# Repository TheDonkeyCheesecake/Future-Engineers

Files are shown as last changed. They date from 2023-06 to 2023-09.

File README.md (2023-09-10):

# Engineers Documentation

Repository containing the engineering elements and details of Team Asparagus from Canada, participating in the 2023 WRO Future Engineers competition.
***
## Repository Content

- `models` - 3D printable files designed by us
- `others` - other essential files
- `schemes` - schematics of our robot's electrical systems
- `src` - main and other programs to run/control software
- `t-photos` - one serious and one funny photo
- `v-photos` - photos of our robot from each angle
- `video` - YouTube link of our robot running each program on the game field
***
## Team Members

- Weston Law, 15, [westonlaw@hotmail.com](mailto:westonlaw@hotmail.com)
- Brian Yin, 15, [brianyin256@gmail.com](mailto:brianyin256@gmail.com)
- Eric Rao, 15, [ericrao08@gmail.com](mailto:ericrao08@gmail.com)

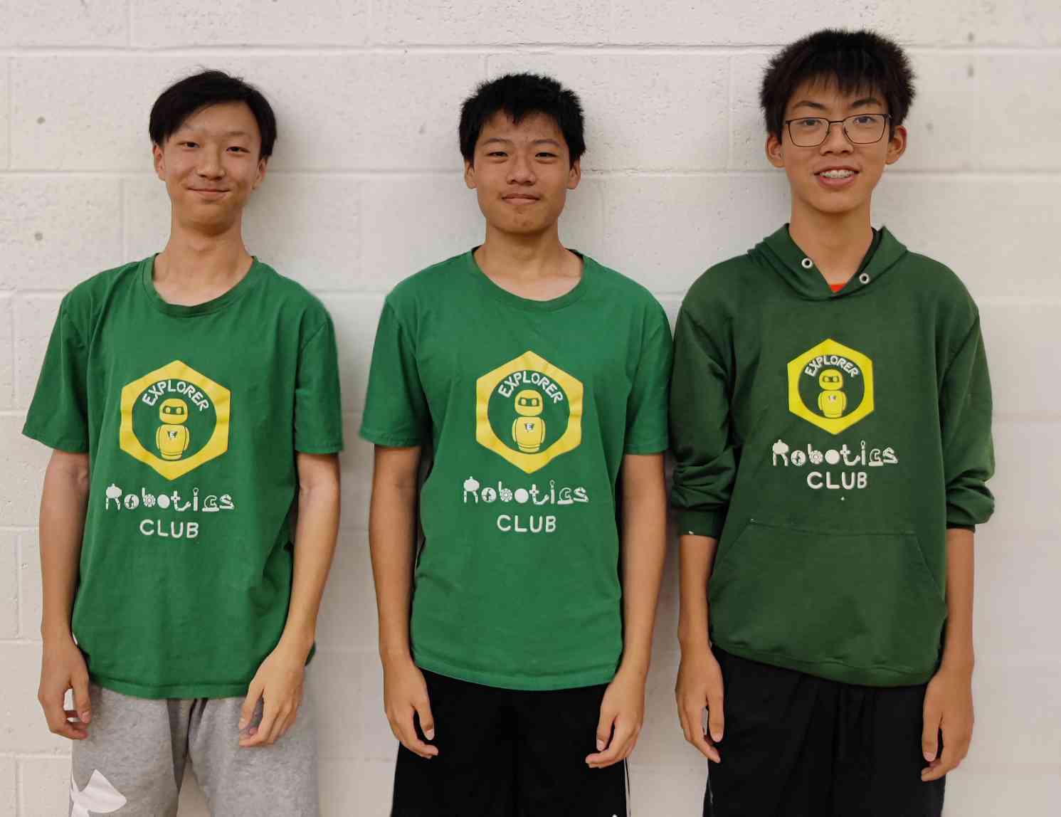
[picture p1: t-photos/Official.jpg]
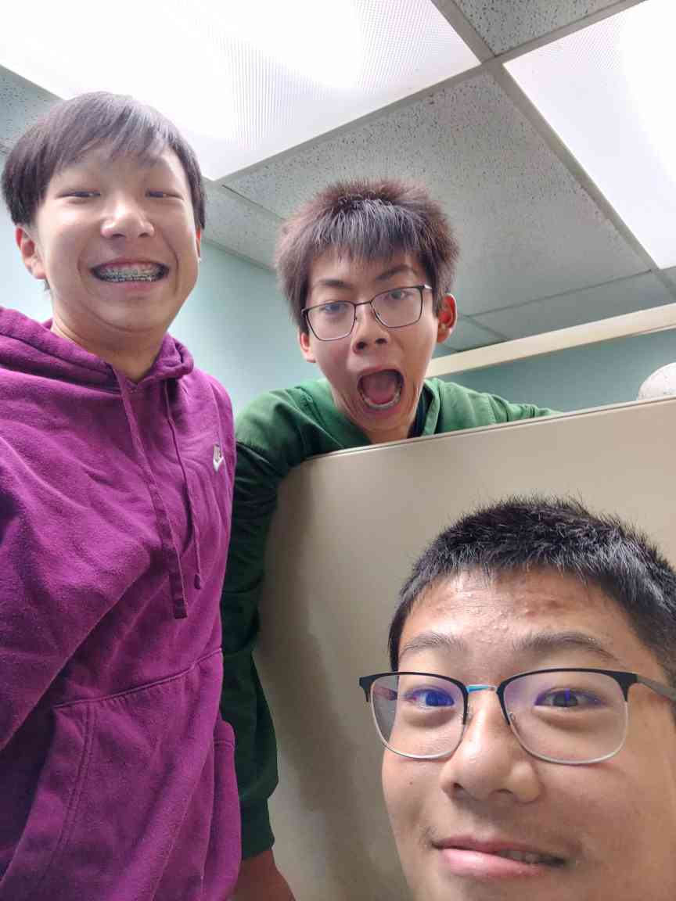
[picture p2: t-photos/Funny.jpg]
 

***Weston (left), Brian (middle), Eric (right)***

***
## Hardware List and Assembly

### Parts List

- [LaTrax Rally RC Car Chassis](https://latrax.com/products/rally)
- [Arduino UNO R3 Controller Board + wires/cables](https://www.amazon.ca/gp/product/B01D8KOZF4/ref=ppx_yo_dt_b_search_asin_image?ie=UTF8&psc=1)
- [Vemico Raspberry Pi 4 Board + Fan](https://www.amazon.ca/gp/product/B09WXRCYL4/ref=ppx_yo_dt_b_search_asin_title?ie=UTF8&psc=1)
- [SanDisk 64GB Ultra microSD Card](https://www.amazon.ca/gp/product/B073JYVKNX/ref=ppx_yo_dt_b_search_asin_title?ie=UTF8&th=1)
- [PiSugar S Pro 5000 mAh Lithium Battery + PiSugar Module Platform Attachment](https://www.amazon.ca/Portable-Platform-Raspberry-Accessories-handhold/dp/B097RCFHD2)
- [HobbyWing Quicrun 2435 4500Kv Brushless Motor](https://www.xtremerc.ca/products/quicrun-wp-10bl60-waterproof-esc-1-10-car-sensorless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)
- [Hobbywing Quicrun WP-16BL30 ESC](https://www.xtremerc.ca/products/hobbywing-quicrun-wp-16bl30-waterproof-1-18th-scale-brushless-esc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)
- [Hosim 7.4V 1600mAh 25C Li-Po Rechargeable Battery](https://www.amazon.ca/Hosim-2pcs-1600mAh-Connector-Li-Polymer/dp/B098QSLJKV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)
- [LoveRPi Wide Angle Camera + CSI Cable](https://www.amazon.ca/gp/product/B07KF6QVPY/ref=ppx_yo_dt_b_search_asin_title?ie=UTF8&psc=1)
- [DKARDU DPST Switch](https://www.amazon.ca/gp/product/B09TKMR8J4/ref=ppx_yo_dt_b_search_asin_title?ie=UTF8&psc=1)

Our 3D-printed parts weigh roughly 75 grams, which is around $2.50 worth of filament. They consist of a platform and pieces to create a camera mount, printed by a Bambu Lab P1P 3D printer.

Total Cost: `$182.84` + `$57.99` + `$229.99` + `$13.36` + `$39.99` + `$49.99` + `$44.99` + `$39.99` + `$13.40` + `$14.49` + `$2.50` respectively = `$689.04` and `$778.61` with tax. (prices in CAD)
***
### Assembly

#### Mobility

We used a prebuilt RC car chassis and made modifications to integrate the rest of our components onto the body of the car, including a new DC motor, a 3D printed platform, and circuit boards (all parts can be found in the Parts List above). In addition, the receiver that allows the car to be controlled remotely was removed, as it was unnecessary and took up space.

The robot moves through two different motors; a `HobbyWing Quicrun 2435 4500Kv Brushless Motor` for driving and a servo motor for steering. The servo motor we use came attached to the prebuilt base, but we changed out the DC motor. The new DC motor is attached similarly to the original, under the 3D printed platform, and takes up roughly the same amount of space. It is held tightly with a metal bracket and screw to prevent it from moving.

We chose this motor as it was one of the highest quality DC motors we could find locally that was of the right size to fit our RC car. This motor provides superior torque to other motors we have tried, an aspect crucial to the function of our car as it helps the car run smoother and avoid cogging at lower speeds. This motor is also brushless meaning higher efficiency and better performance as it doesn't contain the "brushes" that would normally cause friction and reduce the motor's efficiency. 

Unfortunately, even with the higher quality motor, our car still suffers from cogging occasionally when running at low speeds due to the inevitable weight added to the chassis due to our electromagnetic components, which restricts the motor's movement. 

The other component under the platform is the ESC `(electronic speed controller)`, which is wired to and controls the speed of the newly added DC motor. It is also connected to the `Hosim 1600mAh Li-Polymer Battery`, placed right next to it, supplying a sufficient 7.4V.

The motors are controlled by the `Arduino UNO R3 board`, placed on top of the platform using standoffs.

To connect the Arduino, ESC, DC motor, and servo motor, we use a custom-designed perfboard which all the wires plug into to form a circuit. The Arduino uses two PWM `(pulse width modulation)` ports to control the signals sent to both of the motors and an additional port to ground the circuit. The motors use 3 ports/wires each for power, signal, and ground. 

The DC motor is wired to and receives power directly from the ESC (which is connected to the battery), but the servo motor receives it from a BEC `(battery eliminator circuit)` inside the ESC, which is designed to provide a regulated and constant voltage supply to power low-power electronics, such as the servo motor.
***
#### Power and Sensing

Beside the Arduino Board is the `Vemico Raspberry Pi 4 Board`, along with a fan for cooling and a `SanDisk 64GB Ultra microSD Card` to hold our programs. Wired and mounted on top of it is the `PiSugar Module Platform Attachment`, which also is fed power from the `PiSugar S Pro 5000 mAh Lithium Battery`. The battery provides 3.7V, which is then converted to 5V using a voltage regulator to meet the operating voltage requirement of the Raspberry Pi.

We use two separate batteries for the ESC and Raspberry Pi to manage their battery lives independently, as they have different power/voltage requirements. It avoids the problem of having one circuit taking too much power from the battery and leaving an inadequate amount for the other.

The last component is the `LoveRPi Wide Angle Camera`, which is mounted with the help of a custom 3D-printed stand and is wired to the Raspberry Pi through a CSI cable. Although it is more complicated to use, we decided it would be more power-efficient than multiple ultrasonic/colour sensors.

The Raspberry Pi is placed on top of a black box frame specifically made for it, holding it squarely in place, while also housing the fan inside to prevent the Raspberry Pi from overheating.

A `DPST switch` connects to the circuits of both the Raspberry Pi and the ESC, making it possible to turn on both the Raspberry Pi and ESC with one switch. This was done to satisfy the condition of having one power switch to turn on all the components of the car.

#### Photos
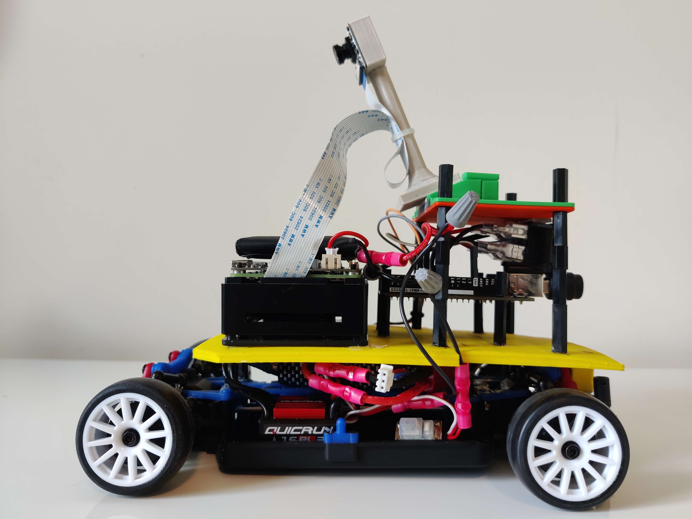
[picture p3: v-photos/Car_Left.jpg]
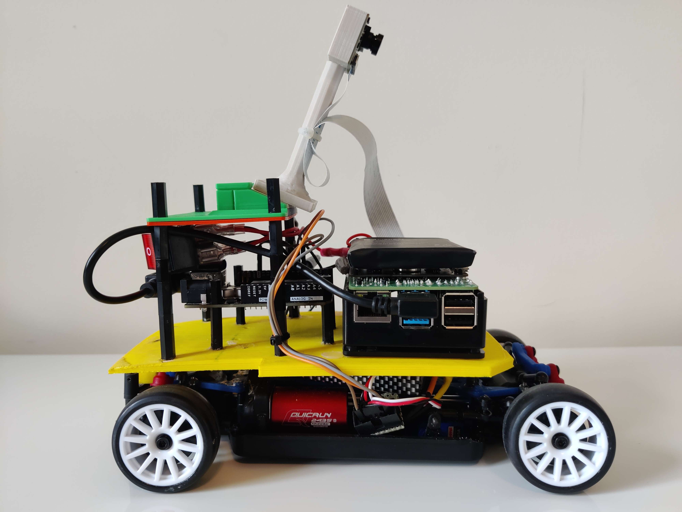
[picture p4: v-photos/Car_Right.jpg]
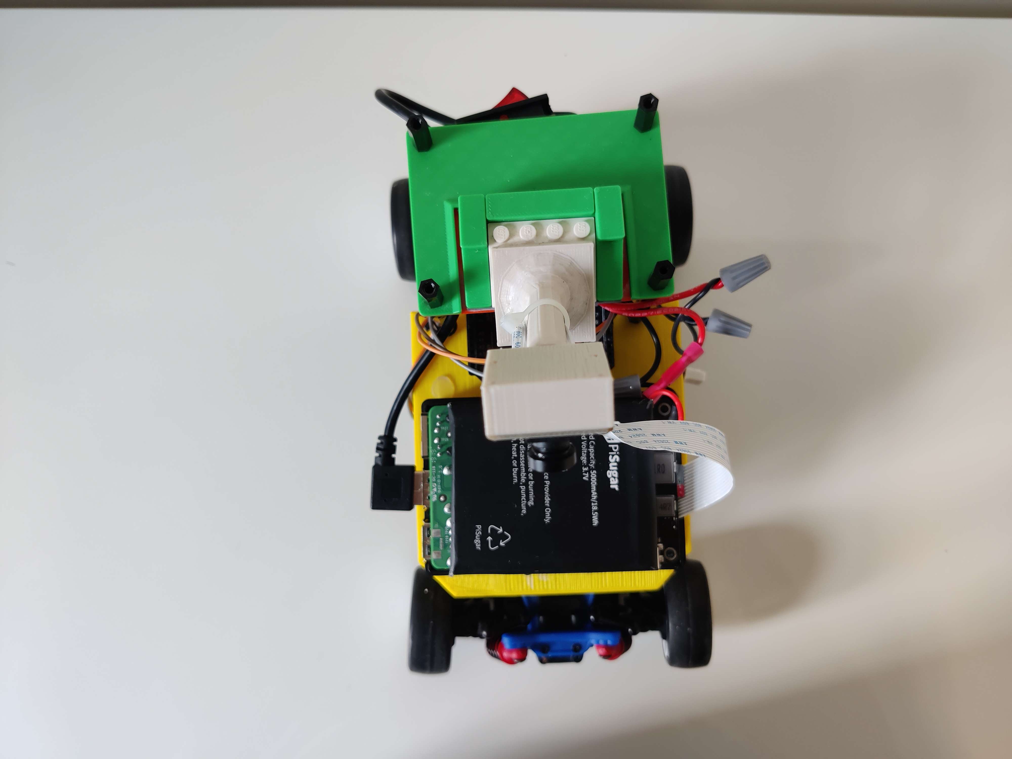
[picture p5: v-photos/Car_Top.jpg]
  

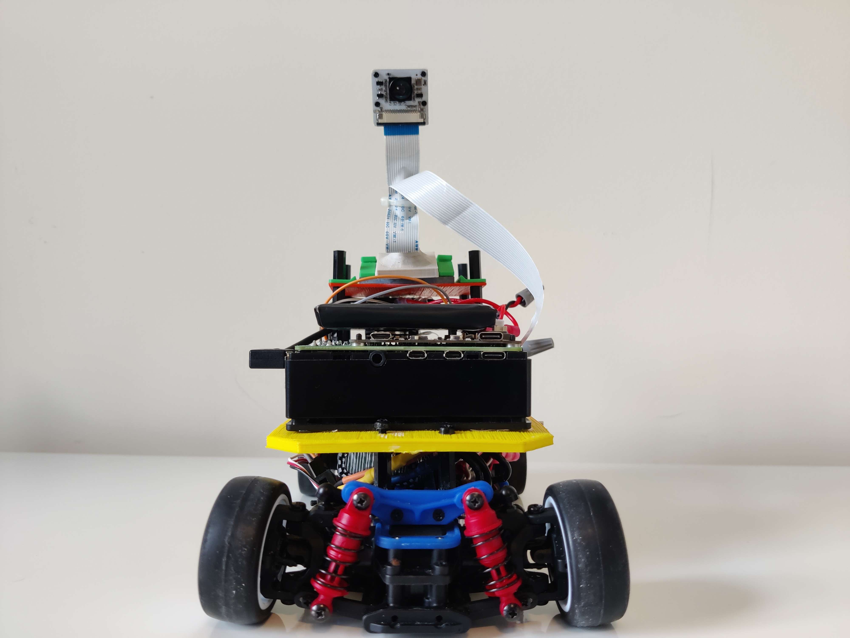
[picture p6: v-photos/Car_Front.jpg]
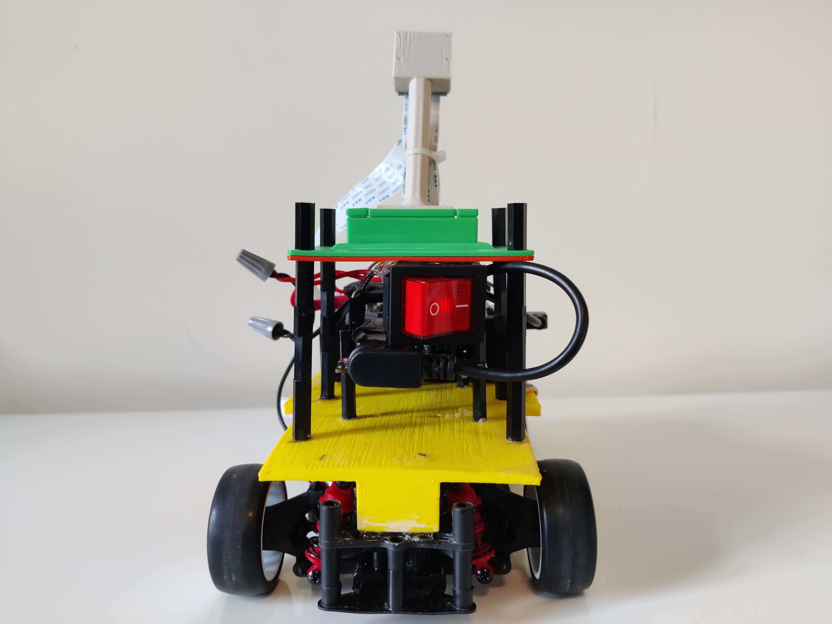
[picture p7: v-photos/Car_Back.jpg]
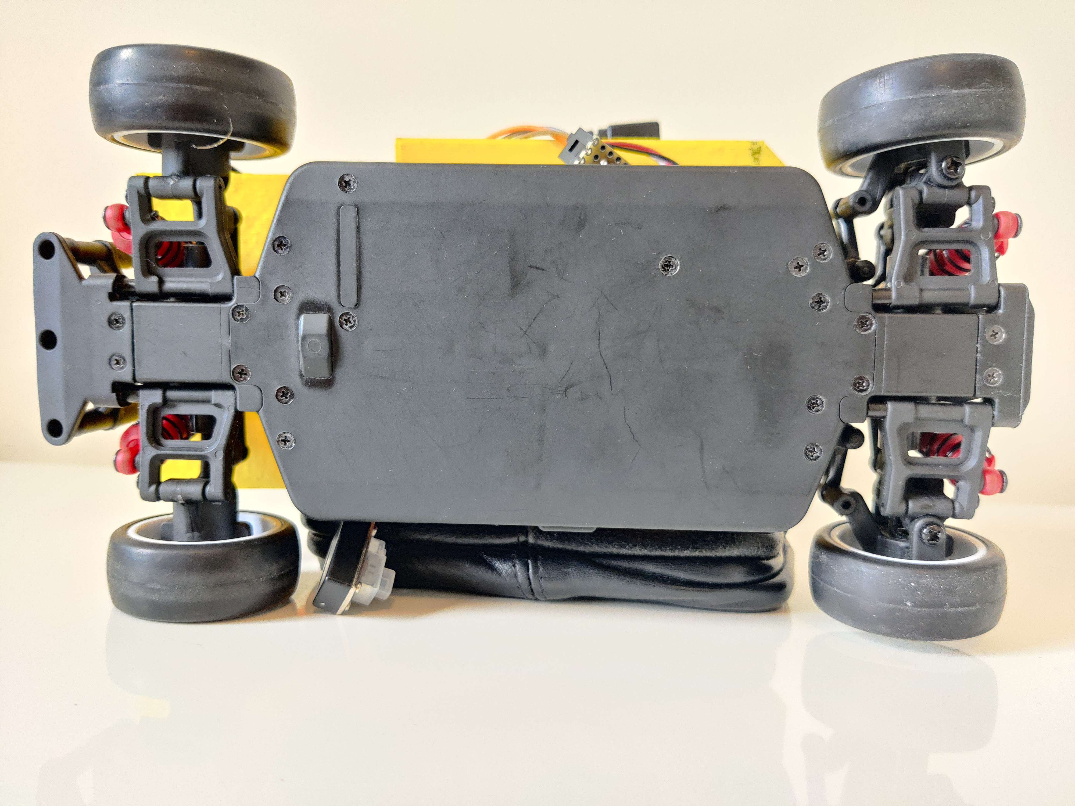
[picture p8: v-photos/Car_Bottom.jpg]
  

#### Schematic
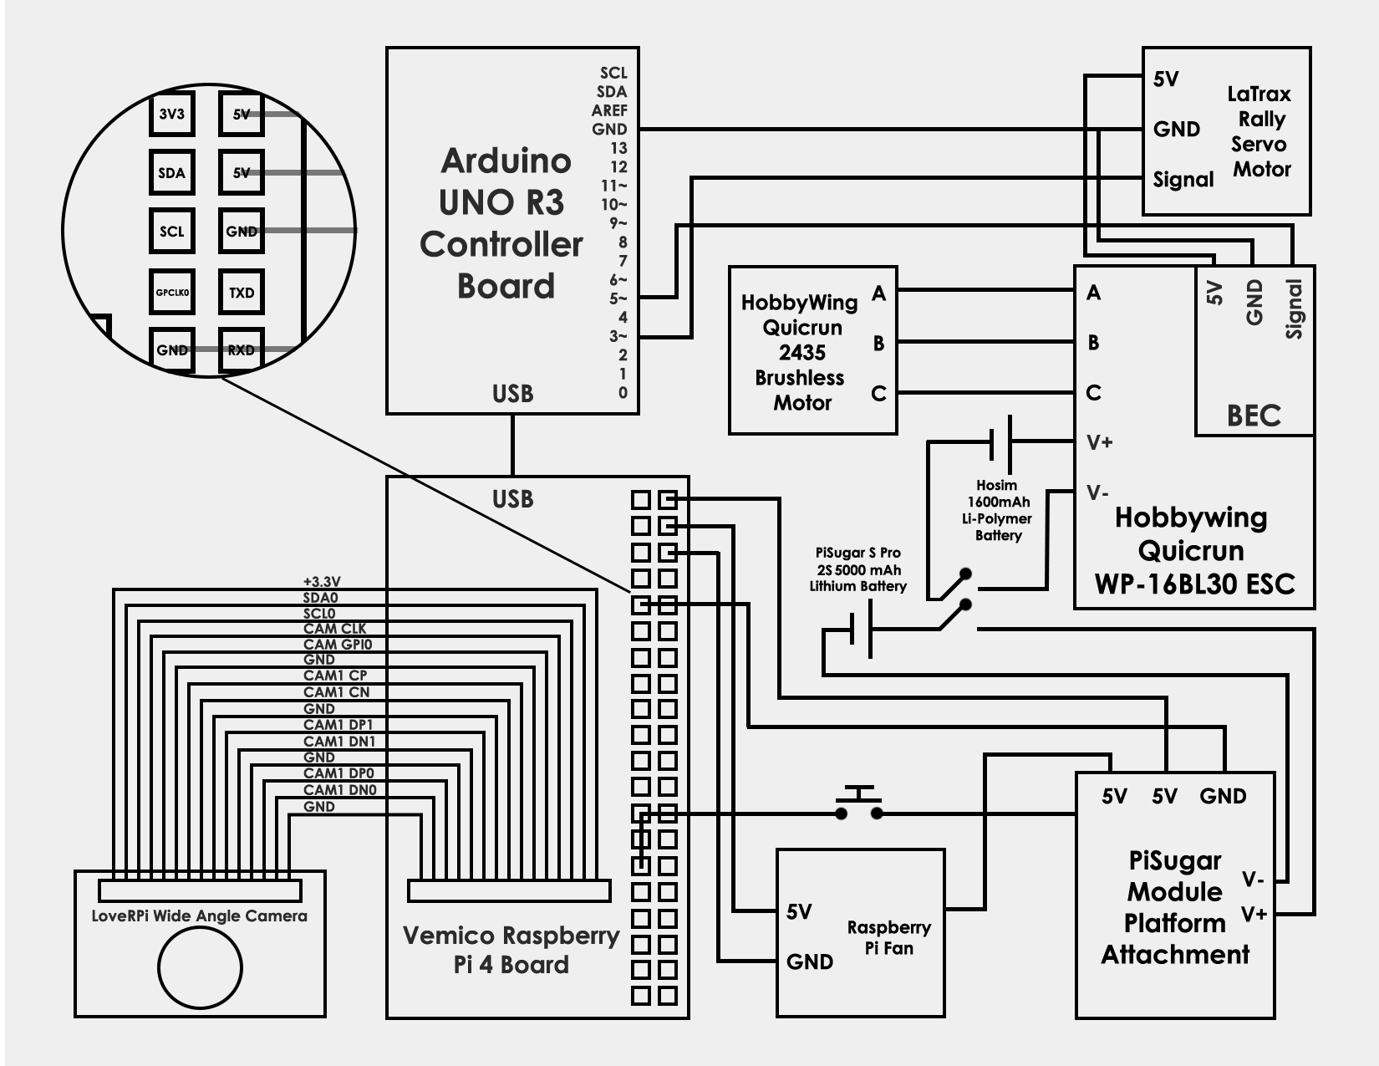
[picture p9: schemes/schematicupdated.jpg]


***

## Initialization and Connection Process

Our Raspberry Pi setup involves downloading the Raspberry Pi OS, writing it to a microSD card using Raspberry Pi Imager ([Download Here](https://www.raspberrypi.com/software/)), and configuring SSH and Wi-Fi. After inserting the SD card, powering up the Pi, and identifying its IP address on the network, we can remotely access it via PuTTY ([Download Here](https://www.putty.org)) for SSH and VNC Viewer ([Download Here](https://www.realvnc.com/en/connect/download/viewer/)) for remote desktop control.
***
## Program Arrangement and Software Elements

Our SBC `(single board computer)` is the Vemico Raspberry Pi 4 Board, which operates on Raspberry Pi OS. Our SBM `(single board microcontroller)` is the Arduino UNO R3 Controller Board. 

Put simply, the Arduino controls the movement, and the Raspberry Pi handles the algorithms and provides the Arduino with the signals to write to the motors. The Raspberry Pi is connected to the Arduino through a USB-A to USB-B cable and communicates with the Arduino through serial communication.

We use Python for the Raspberry Pi code and a variant of C++ designed for Arduino for the Arduino code.
***
### Image Processing

#### Libraries in use:

- `OpenCV` (for computer vision)
- `picamera2` (for camera control)
- `serial` (for serial communication)
- `RPi.GPIO` (for GPIO control on the Raspberry Pi)
- `numpy` (for numerical operations)

The camera captures an image which is first converted from BGR (colour) to grayscale using OpenCV. Binary thresholding is applied to create a binary image, which emphasizes the lanes by setting pixel values to white for areas of interest (walls) and black (other). The script detects the contours of the left and right lanes using the thresholded binary image. The contours are extracted within specific regions of interest `(ROIs)` defined earlier in the code. 

The following algorithms are only used in the obstacle challenge, which requires slightly more camera vision. A key difference between these programs is the use of HSV `(hue, saturation, and vibrance, a method of colour representation similar to RGB)` to detect colour rather than using grayscale
***
#### Signal Pillar Detection

The program detects the contours of signal pillars (red and green) using colour masks based on their respective HSV colour ranges. The contours are then extracted within a specified ROI for obstacles.
***
#### Corner Detection

Similar to the signal pillar detection, the program detects the blue and orange line contours within another specified ROI using HSV colour ranges and uses this to turn. Since the obstacle challenge requires the robot to frequently navigate close to walls to avoid obstacles, using the same method of turning as the open challenge (mentioned in the next segment) is very inconsistent and can lead to turns at the wrong times.
***
### Open Challenge

Fundamentally, the Open Challenge only has two parts to it; wall steering and turning 90 degrees.

Our wall steering program utilizes our camera to differentiate between the black walls and everything else. However, we don't look at the entire camera feed and rather only focus on three specific areas, which are ROIs as mentioned earlier. 

Two of the three regions of interest are used for wall following while the third region of interest is used for counting turns. These two regions of interest were distinctively chosen so that when the robot is placed in the center of the track, the ROIs will both detect a similar amount of black pixels from the wall. This way, we know we are centered on the track when the two ROIs have similar amounts.

In addition, we also use a PD `(proportional and derivative)` follower algorithm to ensure that we can properly and smoothly adjust back on track based on the difference of pixels between the ROIs. Although the standard is to use a PID follower `(proportional, integral, and derivative)`, the "I" is not necessary for a closed and predictable environment that the game field is.

The second part, turning is pretty simple. When we detect that one ROI has a significantly low number of black pixels, then we turn in that direction, as it means that we are nearing a corner. Once that region of interest returns to a larger number of pixels, we end the turning program and return to the wall-following algorithm.

In the open challenge, instead of using binary thresholding, we create a black mask using HSV colour ranges to extract the contours of the walls in the same way as signal pillar detection. 

This is necessary as we found that binary thresholding is unable to distinguish the blue line and the black walls. This is detrimental to our logic as detecting these extra pixels will cause the car to turn later than it should as it would add unaccounted area to the regions of interest of the walls. 

To keep track of our laps, we count each time the turning program is run, up until 12 (4 corners x 3 laps), and stop the robot once its orientation is relatively straight. We also check to see if our camera sees an orange line while turning through the third region of interest, to ensure that we are at the corner.

[Link to Video](https://www.youtube.com/watch?v=jK7tx4uD-Eg)

[Raw Footage](https://www.youtube.com/watch?v=M5vc-97aYjA)

***
### Obstacle Challenge

The obstacle challenge brings the addition of one more segment of code; obstacle avoidance, along with a change in the turning algorithm.

Avoiding the obstacles first involves finding the signal pillars through the signal pillar detection as explained above. 

We utilize both the x and y coordinates of the signal pillar to determine how to navigate. Both the green and red signal pillars have a different set x-coordinate target on the frame that the x-coordinate of the currently detected signal pillar must reach for the car to pass on the correct side. 

The target of the red pillar is on the left side of the frame as we need to pass on the right and the target of the green pillar is on the right side of the frame as we need to pass on the left. 

We calculate the error by taking the difference between this target x-coordinate and its current x-coordinate. Similar to wall following, we use a PD controller with different P and D values optimized for object avoidance as well as another value that changes the adjustment based on how close the pillar is to the car by tracking the y-coordinate, to adjust the car to avoid the obstacle. 

Once the obstacle exits the region of interest and is no longer detectable, the car will go back to the wall following as explained in the Open Challenge Section until it locates another signal pillar or an orange or blue line to turn. 

During turns, when the camera detects a new signal pillar while not currently detecting a blue or orange line, the turn ends with the number of turns being updated by one with the car switching back to obstacle avoidance. This is done to avoid miscounting turns as our car sometimes sees the next pillar before passing the orange or blue line. 

If the camera does not detect a signal pillar during a turn, we use the same method as the open challenge to end the turn: checking if the area of the lane the car is turning towards has increased past a certain threshold. 

Whenever we pass by a pillar we keep track of its target in a variable, and then when we detect a blue or orange line after 7 turns, meaning we are done with the second lap, we can determine if we continue in the same direction or rotate around in the opposite direction as we can determine the colour of the pillar from its target. 

To turn in the opposite direction. The car performs a three-point turn. Firstly, the car turns left at a sharp angle for a set amount of time. Secondly, the car drives right backward for a set amount of time. Finally, obstacle avoidance begins again as the car drives forward while adjusting its angle to the red pillar which is now in front of the car. 

Once we count 12 laps, we create a timer for 3 seconds if we see a signal pillar at the end of the twelfth turn, and a timer for 2 seconds if we see the lane at the end of the twelfth turn. After the timer runs out, the program ends and the car comes to a stop. 

[Link to Video](https://www.youtube.com/watch?v=Huyf2xZaMBw)

[Raw Footage](https://www.youtube.com/watch?v=n-cj5neDJa4)

***

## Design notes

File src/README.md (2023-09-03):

# Engineers Documentation

Repository containing the engineering elements and details of Team Asparagus from Canada, participating in the 2023 WRO Future Engineers competition.

***

## Repository Content

- `chassis` - details of our robot chassis
- `models` - 3D printable files designed by us
- `schemes` - schematics of our robot's electrical systems
- `src` - main and other programs to run/control software
- `t-photos` - one serious and one funny photo
- `v-photos` - photos of our robot from each angle
- `video` - [YouTube link](https://www.youtube.com/your_video_link) of our robot running each program on the game field
- `others` - other essential files

***

## Team Members

- Brian Yin, 16, [brianyin256@gmail.com](mailto:brianyin256@gmail.com)
- Eric Rao, 15, [ericrao08@gmail.com](mailto:ericrao08@gmail.com)
- Weston Law, 15, [westonlaw@hotmail.com](mailto:westonlaw@hotmail.com)

Team Members

***

## Hardware List and Assembly

***

### Parts List

- [LaTrax Rally RC Car Chassis](https://latrax.com/products/rally)
- [Arduino UNO R3 Controller Board + wires/cables](https://www.amazon.ca/gp/product/B01D8KOZF4/ref=ppx_yo_dt_b_search_asin_image?ie=UTF8&psc=1)
- [Vemico Raspberry Pi 4 Board + Fan](https://www.amazon.ca/gp/product/B09WXRCYL4/ref=ppx_yo_dt_b_search_asin_title?ie=UTF8&psc=1)
- [SanDisk 64GB Ultra microSD Card](https://www.amazon.ca/gp/product/B073JYVKNX/ref=ppx_yo_dt_b_search_asin_title?ie=UTF8&th=1)
- [PiSugar S Pro 5000 mAh Lithium Battery + PiSugar Module Platform Attachment](https://www.amazon.ca/Portable-Platform-Raspberry-Accessories-handhold/dp/B097RCFHD2)
- [HobbyWing Quicrun 2435 4500Kv Brushless Motor](https://www.xtremerc.ca/products/quicrun-wp-10bl60-waterproof-esc-1-10-car-sensorless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)
- [Hobbywing Quicrun WP-16BL30 ESC](https://www.xtremerc.ca/products/hobbywing-quicrun-wp-16bl30-waterproof-1-18th-scale-brushless-esc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)
- [LoveRPi Wide Angle Camera + CSI Cable](https://www.amazon.ca/gp/product/B07KF6QVPY/ref=ppx_yo_dt_b_search_asin_title?ie=UTF8&psc=1)
- [DKARDU DPST Switch](https://www.amazon.ca/gp/product/B09TKMR8J4/ref=ppx_yo_dt_b_search_asin_title?ie=UTF8&psc=1)

Our 3D printed parts weigh roughly 40 grams, which is around 2 dollars of filament cost. They consist of a platform and camera mount, printed by the Bambu Lab P1P printer.

Total Cost: $182.84 + $57.99 + $229.99 + $13.36 + $39.99 + $49.99 + $44.99 + $13.40 + $14.49 + $2 respectively = $649.05 and $733.43 with tax. (prices in CAD)

***

### Assembly

***

#### Mobility

We used a prebuilt RC car chassis and made modifications to integrate the rest of our components onto the body of the car, including a new DC motor, a 3D printed platform, and circuit boards (all parts can be found in *Parts List* above). In addition, the receiver that allows the car to be controlled remotely was removed, as it was unnecessary and took up space.

The robot moves through two different motors; a DC motor for driving and a servo motor for steering. The servo motor we use came attached with the prebuilt base, but we changed out the DC motor. The new motor is attached similarly to the original, under the 3D printed platform, and takes up roughly the same amount of space. It is held tightly with a metal bracket and screw to prevent it from moving.

We chose this motor because there are various YouTube videos of it being implemented on our exact RC car chassis. It is also a similar size to the original motor, making it easier to replace. The new motor is also a brushless motor, as compared to the original which is a brushed motor. Brushless motors work similarly to brushed motors using the same principles of magnetic attraction/repulsion but don't have the "brushes" that would normally cause friction and reduce the efficiency of the motor.

The other component under the platform is the ESC (electronic speed controller), which is wired to and controls the speed of the newly added DC motor. It is also connected to the 1600mAh battery, placed right next to it, supplying a sufficient 7.4V.

The motors are controlled by the Arduino UNO R3 board, placed on top of the platform using standoffs.

To connect all the components together, we use a custom-designed perfboard. The Arduino uses two PWM (Pulse Width Modulation) ports to control the speed of the two motors and an additional port to ground the circuit. The motors use 3 ports/wires each for power, signal and ground.

The DC motor is wired to and receives power directly from the ESC (which is connected to the battery), but the servo motor receives it from a BEC (Battery Eliminator Circuit) inside the ESC, which is designed to provide a regulated and constant voltage supply to power low-power electronics, such as the servo motor.

***

#### Power and Sensing

Beside the Arduino Board is the Vemico Raspberry Pi 4 Board, along with a fan for cooling and a SanDisk 64GB Ultra microSD Card to hold our programs. Wired and mounted on top of it is the PiSugar Module Platform Attachment, which also is fed power from the PiSugar S Pro 5000 mAh Lithium Battery. The battery provides 3.7V which is then converted to 5V using a voltage regulator to meet the operating volt requirement of the Raspberry Pi.

We use two separate batteries for the ESC and Raspberry Pi in order to manage their battery lives independently, as they have different power/voltage requirements. It avoids the problem of having one circuit taking too much power from the battery and leaving an inadequate amount for the other.

The last component is the camera, which is mounted with the help of a custom 3D printed stand and is wired to the Raspberry Pi through a CSI Cable. Although it is more complicated to use, we decided it would be more power-efficient than multiple ultrasonic/color sensors.

The Raspberry Pi is placed on top of a black box frame specifically made for it, holding it squarely in place, while also housing the fan inside to prevent the Raspberry Pi from overheating.

A DPST switch controls the power of the Raspberry Pi and Arduino to satisfy the condition of having one power button.

***

#### Photos

Robot Image 1
Robot Image 2

#### Schematic

Schematic

***

## Initialization and Connection Process

Our Raspberry Pi setup involves downloading the Raspberry Pi OS, writing it to a microSD card using Raspberry Pi Imager [Raspberry Pi Imager](https://www.raspberrypi.com/software/), and configuring SSH and Wi-Fi. After inserting the SD card, powering up the Pi, and identifying its IP address on the network, we can remotely access it via PuTTY [PuTTY](https://www.putty.org) for SSH and VNC Viewer [VNC Viewer](https://www.realvnc.com/en/connect/download/viewer/) for remote desktop control.

***

## Program Arrangement and Software Elements

***

### Image Processing

Libraries in use:

- OpenCV (for computer vision)
- picamera2 (for camera control)
- serial (for serial communication)
- RPi.GPIO (for GPIO control on the Raspberry Pi)
- numpy (for numerical operations)

The captures an image which is first converted from BGR (color) to grayscale using OpenCV. Binary thresholding is applied to create a binary image, which emphasizes the lanes by setting pixel values to black for areas of interest (walls) and white (other). The script detects the contours of the left and right lanes using the thresholded binary image. The contours are extracted within specific regions of interest (ROIs) defined earlier in the code.

***

#### Signal Pillar Detection

The program detects the contours of signal pillars (red and green) using color masks based on their respective HSV color ranges. The contours are then extracted within a specified ROI for obstacles.

***

#### Corner Detection

Similar to the signal pillar detection, the program detects the blue and orange lines using HSV color ranges, and uses this to turn. Since the obstacle challenge requires the robot to turn very frequently, using the same method of turning as the open challenge (mentioned in the next topic) is very inconsistent.

***

### Open Challenge

Fundamentally, the Open Challenge only has two parts to it; wall steering and turning 90 degrees.

Our wall steering program utilizes our camera to differentiate between the black walls and everything else. However, we don't actually look at the entire camera feed and rather only focus on two specific areas, which are ROIs as mentioned earlier. These two regions of interest were distinctively chosen so that when the robot is placed in the center of the track, they will have a similar amount of black pixels from the wall. This way, we know we are on track when the two ROIs have similar amounts.

In addition, we also use a PD (Proportional and Derivative) follower algorithm to ensure that we can properly and smoothly adjust back on track based on the difference of pixels between the ROIs. Although the standard is to use a PID follower (Proportional, Integral and Derivative), the "I" is not necessary for a closed and predictable environment as the game field is.

The second part, turning is pretty simple. When we detect that one ROI has significantly fewer black pixels than the other, then we turn in that direction, as it means that we are nearing a corner. Once that region of interest returns to its usual amount of pixels, we end the turning program and return to wall following.

To keep track of our laps, we count each time the turning program is run, up until 12 (4 corners x 3 laps) and stop the robot. We also check to see if our camera actually sees an orange line while turning, to ensure that we are at the corner.

***

### Obstacle Challenge

The obstacle challenge brings the addition of one more segment of code, being the obstacle avoidance, along with a change of the turning algorithm.

Avoiding the obstacles involves changing the values of P and D in our PD movement control. Rather than following the middle of the track as we usually do, a change in these values allows us to follow closer to either side of the track, avoiding the obstacle.

In order to turn back to the middle of the track, we wait until the obstacle nears the edge of our camera view. Once it reaches a given point on the length of our camera feed, we reset the P and D values to re-center the robot.

We change the turning method in this challenge because the previous one has difficulty working consistently with the number of other turns we do to avoid the obstacles in this challenge. When the robot is on an angle, usually while turning, the previous method can trigger when is isn't supposed to.

***

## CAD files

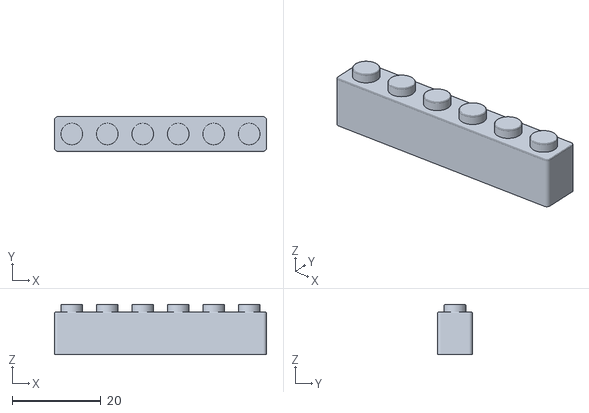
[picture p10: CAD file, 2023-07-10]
models/Brick 1x6.stl
47.8 x 7.80 x 11.3

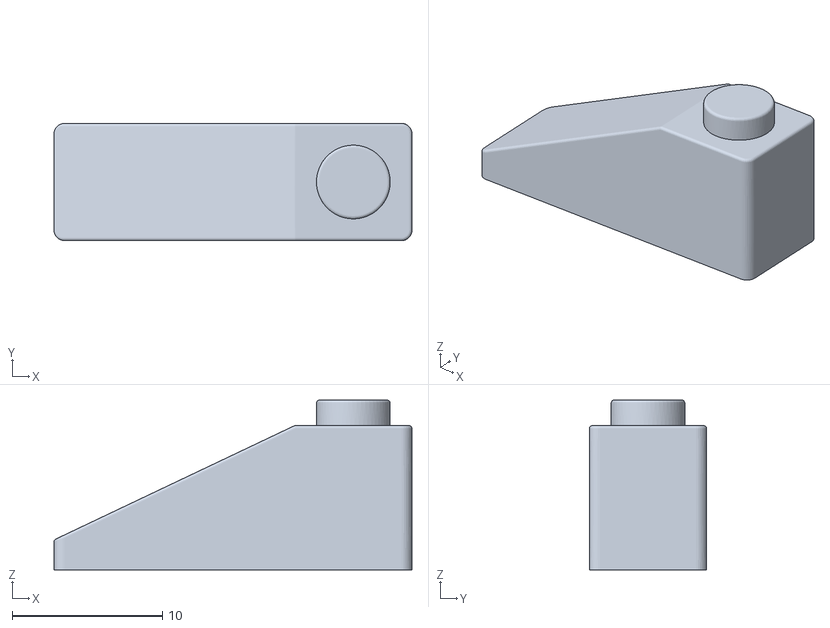
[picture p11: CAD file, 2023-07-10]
models/Slope 25 3x1.stl
23.8 x 7.80 x 11.3

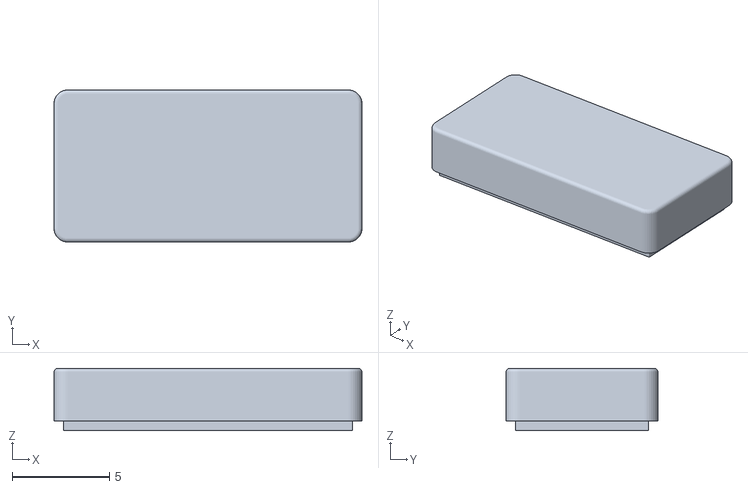
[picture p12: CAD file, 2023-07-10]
models/Tile 1x2.stl
15.8 x 7.80 x 3.20

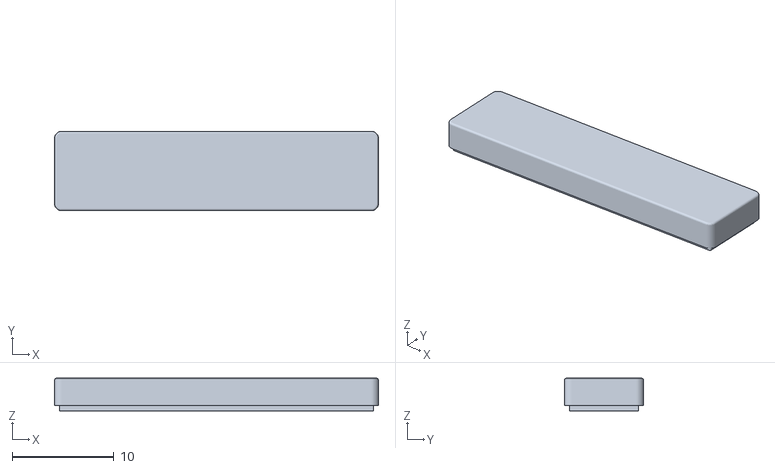
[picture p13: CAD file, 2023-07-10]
models/Tile 1x4.stl
31.8 x 7.80 x 3.20

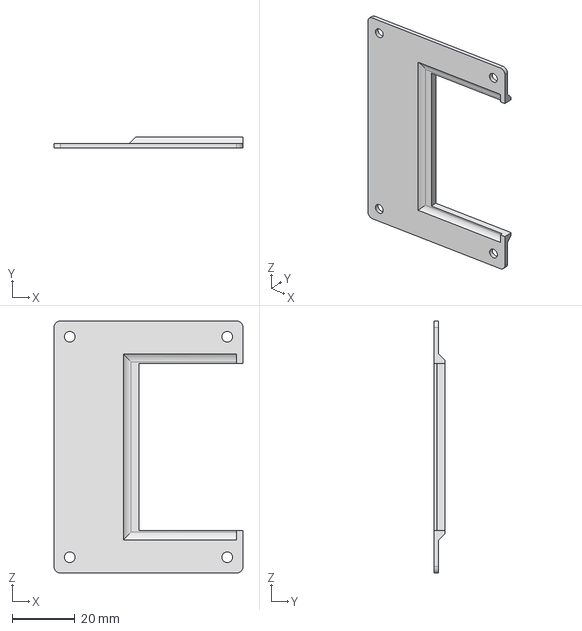
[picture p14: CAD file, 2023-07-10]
models/CameraTableCover.stp
60.0 x 3.50 x 80.0 mm

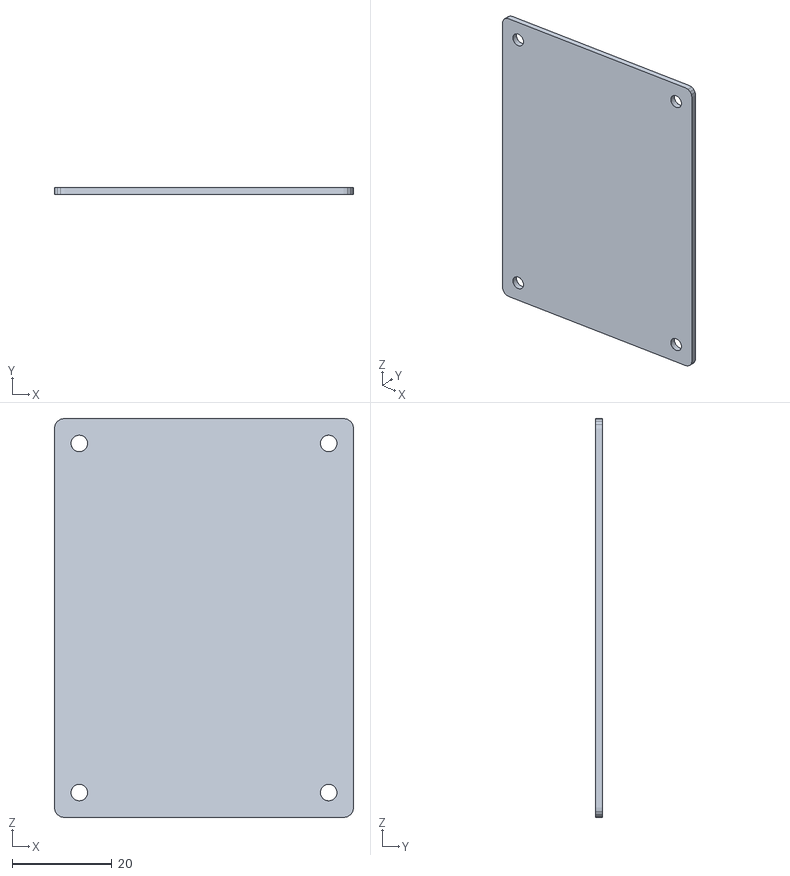
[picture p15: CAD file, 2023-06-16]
models/CameraTable.stl
60.0 x 1.50 x 80.0

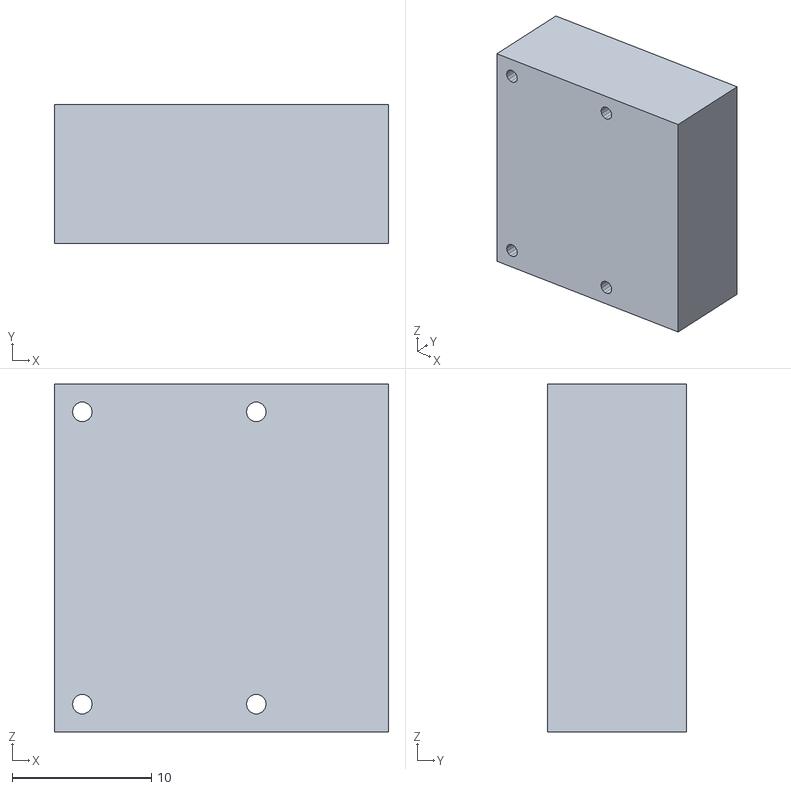
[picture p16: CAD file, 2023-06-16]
models/CameraMount3.stl
24.0 x 10.0 x 25.0

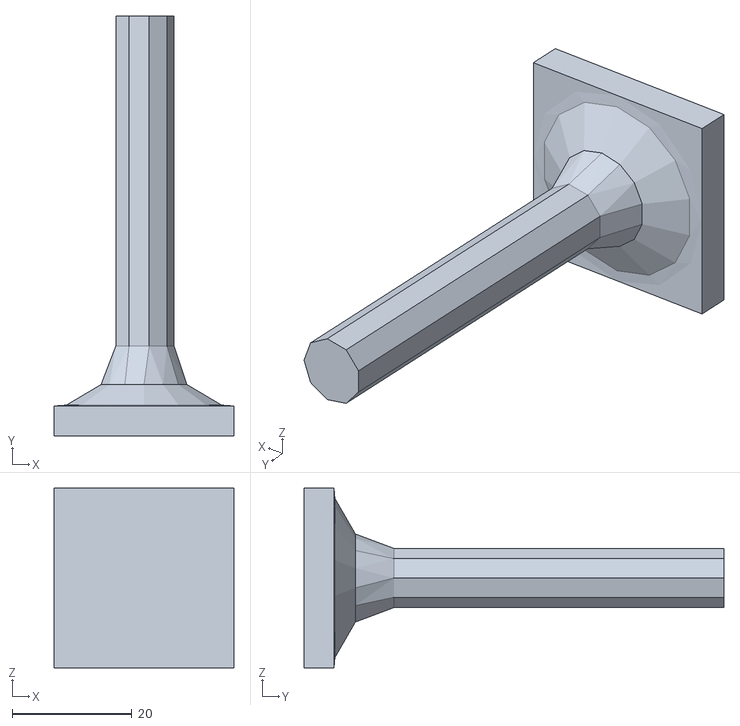
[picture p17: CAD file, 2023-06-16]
models/CameraMount2.stl
30.0 x 70.0 x 30.0

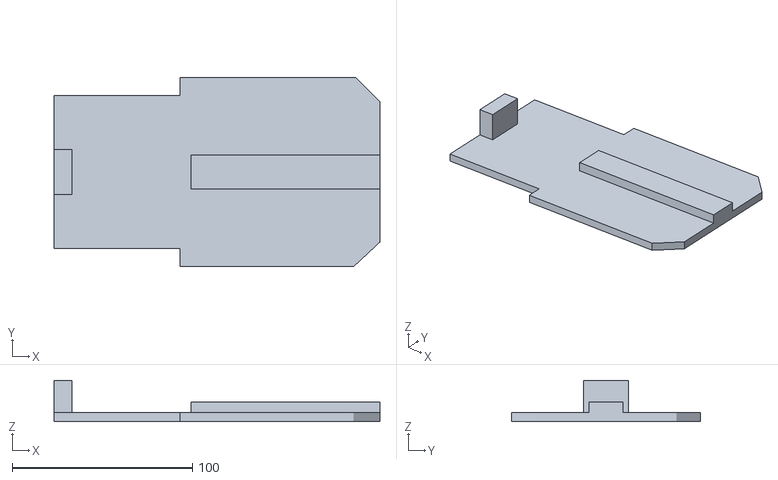
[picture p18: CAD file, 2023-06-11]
models/Spectacular Kup-Robo.stl
181.0 x 105.0 x 23.0

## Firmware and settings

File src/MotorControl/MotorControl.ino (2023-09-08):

#include <Servo.h>

//declare servo objects for DC motor and servo motor
Servo BLDCMotor;
Servo servoMotor;

//char array for storing signals from raspberry pi 
char command[5]; 

//set up function
void setup(){
  
  Serial.begin(115200); //begin Serial communication at baud rate of 115200
  servoMotor.attach(6); //set servo pin
  servoMotor.write(90); //reset servo angle
  BLDCMotor.attach(5, 1000, 2000); //set DC motor pin
  BLDCMotor.writeMicroseconds(1500); //reset DC motor speed
  pinMode(LED_BUILTIN, OUTPUT); //initialize the built in LED for output
  delay(6000);

}

void loop(){
  //if signal is available
  while(Serial.available() > 0)
  {

    //read signal and convert to 4-digit integer
    int size = Serial.readBytes(command, 4);
    command[4] = '\0';
    int val = atoi(command); 
    
    //if signal is within 1000 and 2000, write the signal to DC motor
    if(val <= 2000 && val >= 1000)
    {
      BLDCMotor.writeMicroseconds(val);
    }
    //if signal is within 2001 and 2180, write the signal to servo motor
    else if(val > 2000 && val <= 2180)
    {
      servoMotor.write(val - 2000);
    //if 9999 is the signal, turn the built-in LED on to show car is in waiting state
    } else if(val == 9999) {
      digitalWrite(LED_BUILTIN, HIGH); 
    }
    
  }
}

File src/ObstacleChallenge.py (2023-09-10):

#import necessary libraries
import cv2
from picamera2 import Picamera2
import serial
from time import sleep
import time
import RPi.GPIO as GPIO
import numpy as np

#function used to send signals to arduino to control speeds of the dc motor and the angle of the servo motor
def write(value): 
    ser.write((str(value)).encode('utf-8'))
    print("signal sent:", value)

#function which displays the Regions of Interest on the image
def displayROI():
    image = cv2.line(img, (ROI1[0], ROI1[1]), (ROI1[2], ROI1[1]), (0, 255, 255), 4)
    image = cv2.line(img, (ROI1[0], ROI1[1]), (ROI1[0], ROI1[3]), (0, 255, 255), 4)
    image = cv2.line(img, (ROI1[2], ROI1[3]), (ROI1[2], ROI1[1]), (0, 255, 255), 4)
    image = cv2.line(img, (ROI1[2], ROI1[3]), (ROI1[0], ROI1[3]), (0, 255, 255), 4)
    
    image = cv2.line(img, (ROI2[0], ROI2[1]), (ROI2[2], ROI2[1]), (0, 255, 255), 4)
    image = cv2.line(img, (ROI2[0], ROI2[1]), (ROI2[0], ROI2[3]), (0, 255, 255), 4)
    image = cv2.line(img, (ROI2[2], ROI2[3]), (ROI2[2], ROI2[1]), (0, 255, 255), 4)
    image = cv2.line(img, (ROI2[2], ROI2[3]), (ROI2[0], ROI2[3]), (0, 255, 255), 4)

    image = cv2.line(img, (ROI3[0], ROI3[1]), (ROI3[2], ROI3[1]), (0, 255, 255), 4)
    image = cv2.line(img, (ROI3[0], ROI3[1]), (ROI3[0], ROI3[3]), (0, 255, 255), 4)
    image = cv2.line(img, (ROI3[2], ROI3[3]), (ROI3[2], ROI3[1]), (0, 255, 255), 4)
    image = cv2.line(img, (ROI3[2], ROI3[3]), (ROI3[0], ROI3[3]), (0, 255, 255), 4)
    
    image = cv2.line(img, (ROI4[0], ROI4[1]), (ROI4[2], ROI4[1]), (0, 255, 255), 4)
    image = cv2.line(img, (ROI4[0], ROI4[1]), (ROI4[0], ROI4[3]), (0, 255, 255), 4)
    image = cv2.line(img, (ROI4[2], ROI4[3]), (ROI4[2], ROI4[1]), (0, 255, 255), 4)
    image = cv2.line(img, (ROI4[2], ROI4[3]), (ROI4[0], ROI4[3]), (0, 255, 255), 4)

#function to bring the car to a stop
def stopCar():
    #write(1438)
    #sleep(1)
    write(2098)
    write(1500)
    cv2.destroyAllWindows()

if __name__ == '__main__':

    #initialize camera
    picam2 = Picamera2()
    picam2.preview_configuration.main.size = (640,480)
    picam2.preview_configuration.main.format = "RGB888"
    picam2.preview_configuration.controls.FrameRate = 60
    picam2.preview_configuration.align()
    picam2.configure("preview")
    picam2.start()

    #initialize serial port
    ser = serial.Serial('/dev/ttyACM0', 115200, timeout = 1) 
    ser.flush()

    #initialize GPIO pins for button
    GPIO.setwarnings(False)
    GPIO.setmode(GPIO.BOARD)
    GPIO.setup(5, GPIO.IN, pull_up_down=GPIO.PUD_UP)

    #set the target x coordinates for each red and green pillar
    redTarget = 160
    greenTarget = 480

    #variable that keeps track of the target of the last pillar the car has passed
    lastTarget = 0

    #boolean that is used for when the car has to turn around to the opposite direction so the car can complete the last lap the other way around
    reverse = False

    #boolean storing the only direction the car is turning during the run
    turnDir = "none" 
    
    #lists storing coordinates for the regions of interest to find contours of different areas
    #ROI1: for finding left lane
    #ROI2: for finding right lane
    #ROI3: for finding signal pillars
    #ROI4: for detecting blue and orange lines on mat
    # order: x1, y1, x2, y2
    ROI1 = [25, 190, 330, 300]
    ROI2 = [330, 165, 640, 285]
    ROI3 = [redTarget - 50, 190, greenTarget + 50, 400]
    ROI4 = [200, 350, 440, 400]

    #booleans for tracking whether car is in a left or right turn
    lTurn = False
    rTurn = False
  
    kp = 0.005 #value of proportional for proportional steering
    kd = 0.005  #value of derivative for proportional and derivative sterring

    cKp = 0.17 #value of proportional for proportional steering for avoiding signal pillars
    cKd = 0.17 #value of derivative for proportional and derivative sterring for avoiding signal pillars
    cy = 0.075 #value used to affect pd steering based on how close the pillar is based on its y coordinate
  
    straightConst = 98 #angle in which car goes straight
    exitThresh = 4000 #if area of both lanes is over this threshold car exits a turn
  
    angle = 2098 #variable for the current angle of the car
    prevAngle = angle #variable tracking the angle of the previous iteration
    tDeviation = 50 #value used to calculate the how far left and right the car turns during a turn
    sharpRight = straightConst - tDeviation + 2000 #the default angle sent to the car during a right turn
    sharpLeft = straightConst + tDeviation + 2000 #the default angle sent to the car during a left turn
    
    speed = 1442 #variable for initial speed of the car
    tSpeed = 1434 #variable for speed of the car during turn to opposite direction
    reverseSpeed = 1615 #variable for speed of the car going backwards

    
    stopTime = 0 #stores the time of when the car begins its stopping progress
    s = 0 #stores for how many seconds the car runs after stopTime
    
    aDiff = 0 #value storing the difference of area between contours
    prevDiff = 0 #value storing the previous difference of contours for derivative steering

    error = 0 #value containing the difference between a pillar's x coordinate and its target x coordinate
    prevError = 0 #stores previous error

    cTarget = 0 #stores the target x coordinate for the current signal pillar, stays 0 if there is no signal pillar
    contX = 0 #stores x value of the current signal pillar
    contY = 0 #stores y value of the current signal pillar
    
    t = 0 #tracks number of turns
    
    tSignal = False #boolean that makes sure that a pillar doesn't affect a turn too early

    sleep(8) #delay 8 seconds for the servo to be ready
    
    write(9999)
    
    #if button is pressed break out of loop and proceed with rest of program
    while True:
        if GPIO.input(5) == GPIO.LOW:
            break
        
    sleep(0.5) 
    
    #write initial values to car
    write(speed) 
    write(angle)

    #main loop
    while True:

        #if s seconds has passed after the car began the stopping process, end the program and stop the car
        if stopTime != 0:
            if time.time() - stopTime > s:
                stopCar()
                break
            
        #reset rightArea, and leftArea variables
        rightArea, leftArea = 0, 0

        #get an image from pi camera
        img = picam2.capture_array()

        #convert to grayscale
        imgGray = cv2.cvtColor(img, cv2.COLOR_BGR2GRAY)

        #threshold image
        ret, imgThresh = cv2.threshold(imgGray, 55, 255, cv2.THRESH_BINARY_INV)

        #find left and right contours of the lanes
        contours_left, hierarchy = cv2.findContours(imgThresh[ROI1[1]:ROI1[3], ROI1[0]:ROI1[2]], 
        cv2.RETR_EXTERNAL, cv2.CHAIN_APPROX_NONE)
    
        contours_right, hierarchy = cv2.findContours(imgThresh[ROI2[1]:ROI2[3], ROI2[0]:ROI2[2]], 
        cv2.RETR_EXTERNAL, cv2.CHAIN_APPROX_NONE)
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

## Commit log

2023-06-11 Added Arduino motor control code
2023-08-13 Update README.md
    i hit the wrong button earlier but i think this works. again im jsut saving it incase but stuff that I gotta check on has a * next to it
2023-08-28 forgot motor battery
